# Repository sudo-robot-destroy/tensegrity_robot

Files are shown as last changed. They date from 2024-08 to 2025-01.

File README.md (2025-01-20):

# tensegrity_robot
A repository to track the development of a robot with tensegrity wheels

## Main Design Goals
The main idea is to investigate making a ground vehicle capable of being dropped from a drone without being damaged with the following requirements:
* The vehicle should also be able to drive over rough terrain like high grass, forest floor and climb steps.
* It should also either be able to drive upside down or easily flip itself over.
* The vehicle should be light weight and made using DIY components like off the shelf parts and 3D printing.

## Background
The first design is motivated by [[1]](https://jiefengsun.github.io/pdfs/spiegel2023shape.pdf).
As mentioned in the paper, some shortcomings of their design are sticks get stuck in wheels since they're open, and it tips over easily since there are only two wheels. The first design trial will use similar wheels but will have 4 wheels in a skid steer layout. If stuck sticks are a problem I might look into using closed wheels although I'm not sure if they're work great. 

Construction of tensegrity wheels is detailed in [[2]](http://best.berkeley.edu/wp-content/uploads/2017/09/DETC2017-68264-1.pdf).

## Rough ideas
* The wheels will be TPU and carbon fiber rod.
* The rest of the body will be a combination of carbon fiber rod and 3D printed TPU and PETG parts.  
* The first design will use simple electronics:  
  * an RF receiver
  * 4-in-1 ESC
  * Two brushless motors for drive
  * A single servo for collapsing the wheels?
  * A lipo battery (3s?)

## First design attributes
For the first design, I'll just copy the wheels from [1] as much as possible, here is what they used:  
### Wheels: 
* Carbon rod diameter: 2 mm  
* Carbon rod length (l<sub>r</sub>): 130 mm, 6 rods/wheel so 24 are needed.  
* Rod caps: abrasion-resistant TPU - Cheetah 95 A  
* Rod cap length: 12 mm
* Cable material: TPU - Ninja-flex 85 A  
* Wheel hub material: Nylon-X (carbon fiber-enhanced filament)  
* Cable cross thickness: 1.5 mm  
* Cable width: 1 mm 
* Cable length (printed, 0.9(0.6l<sub>r</sub>)): 70.2 mm  

### Collapsing mechanism:  
* Motor:[Pololu: 1595](https://www.pololu.com/product/1595) (stall torque - 12 kgcm) 
* Cable: Nylon

### Drive train:
* Drive motors: [Pololu: 4794](https://www.pololu.com/product/4794) with 3:1 extra  
* Stall torque: 5.5 kgcm x 3 = 16.5 kgcm
* Drive bearings: [Uxcell: 626-2RS](https://www.amazon.com/uxcell-626-2RS-Bearing-6x19x6mm-Bearings/dp/B07TLKGDJ6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) 
* Battery: 2S Lipo
* Motor driver: [Pololu: 2135](https://www.pololu.com/product/2135) (also used for collapsing) 

## Shopping list
* Carbon fiber rods: [400 mm x 10 from Fielect for $12.99](https://www.amazon.com/Fielect-Diameter-Carbon-Straight-Airplane/dp/B083LC917H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)  
* TPU, 85A: [Siraya Tech Flex TPU for $31.99](https://www.amazon.com/Siraya-Tech-Flex-Filament-Moisture-Resistant/dp/B0CP213ZMG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) 

## Print details
* Rod end-caps
  * 12 per wheel so 48 total...maybe, unless there are special ones that connect to hubs. 
  * No supports
  * Standard .2 profile
  * Profile for tight rod fit starts with a 2mm hole, then a 1 degree draft. The crushed ribs go .25 mm into the 2mm rods. It might be a little too tight, I have to hammer them in.  
  * Currently printed with PLA 
* Cable section
  * TPU 85A
  * Used 3 walls but mainly just to do a solid infill that way. 
  * 8 per wheel? 

## Test prints
Here was the first tensegrity ball I made - I was able to throw it on concrete as hard as I can without any damage:

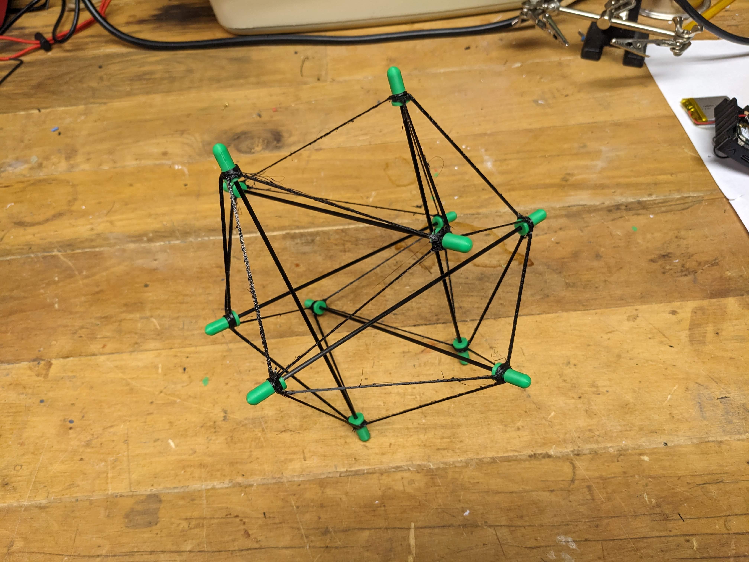
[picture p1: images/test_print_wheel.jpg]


## TO-DOs:
* Buy GT2 belt components
  * wheel span is 200 mm so belts need to be around 100mm each. 
  * 6mm wide
  * 2mm pitch.  
  * It looks like the list them by the outer perimeter. I estimate 243.33 for a 20T pulley so call it 250mm
  * That'd be a 250-2GT-6 belt. Ordered 12Jan2025
  * 20 tooth is the popular small pulley size. 
* Make the wheel hub part
  
## References:
[1] "A Shape-Changing Wheeling and Jumping Robot Using Tensegrity Wheels and Bistable Mechanism" https://jiefengsun.github.io/pdfs/spiegel2023shape.pdf

[2] "Modular Elastic Lattic Platform for Rapid Prototyping of Tensegrity Robots" http://best.berkeley.edu/wp-content/uploads/2017/09/DETC2017-68264-1.pdf

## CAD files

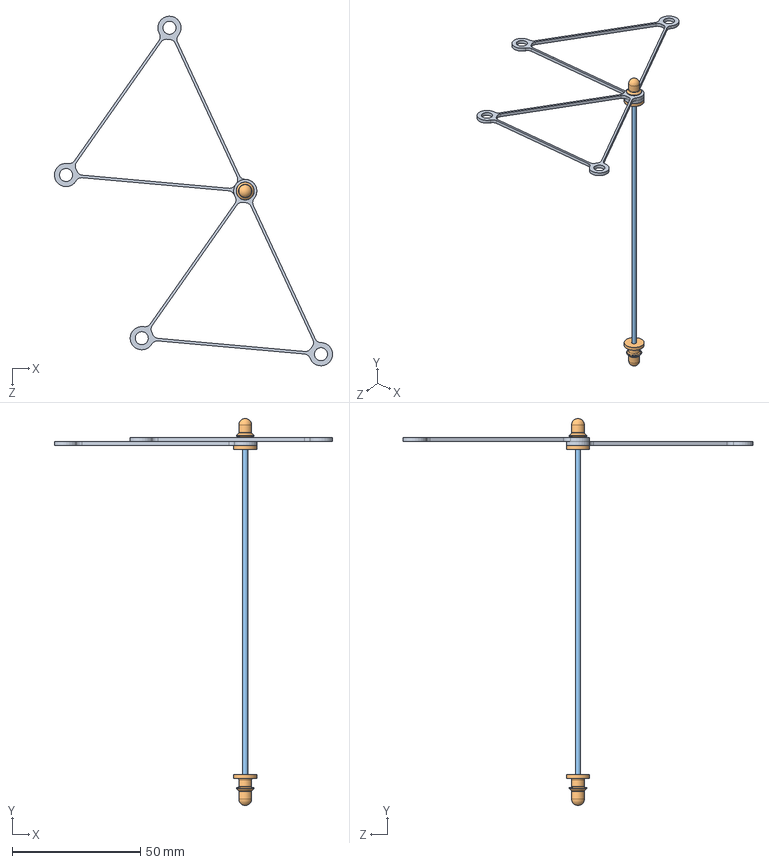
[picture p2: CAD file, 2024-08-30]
developmental_assemblies/rod_end_assembly.SLDASM
108.6 x 151.0 x 136.4 mm
tensegrity_rods_2mm_130mm
rod_end_cap x 2
tensegrity_cable_section x 2

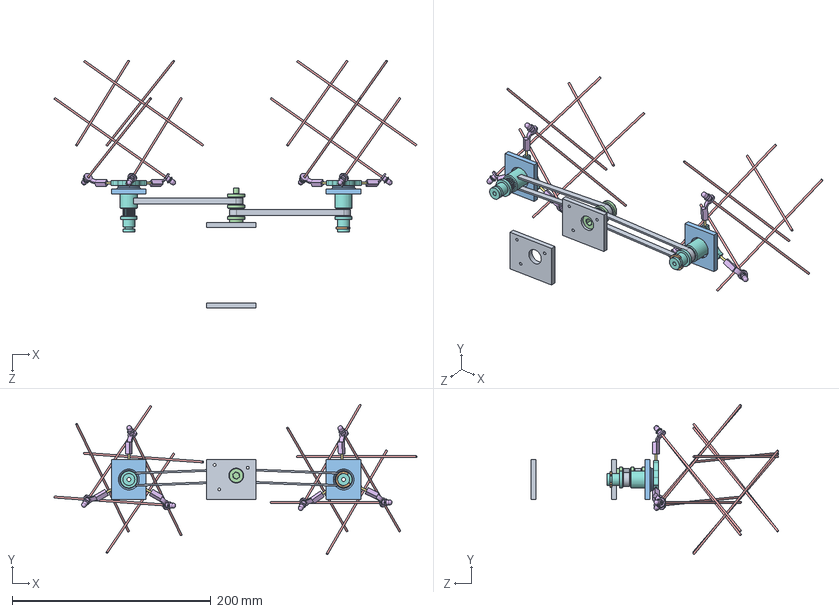
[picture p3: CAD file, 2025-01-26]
main_assembly.SLDASM
365.4 x 151.3 x 249.1 mm
motor_mount_L x 2
wheel_hub x 2
hub_rods_2mm_dia x 6
rod_end_cap_hub x 6
tensegrity_rods_2mm_130mm x 12
gt2_pulley_20T_double
wheel_axle_bearing x 2
custom-98543A116_Side-Mount External Retaining Rings x 2
250-GT2-belt-20Tpulleys x 2

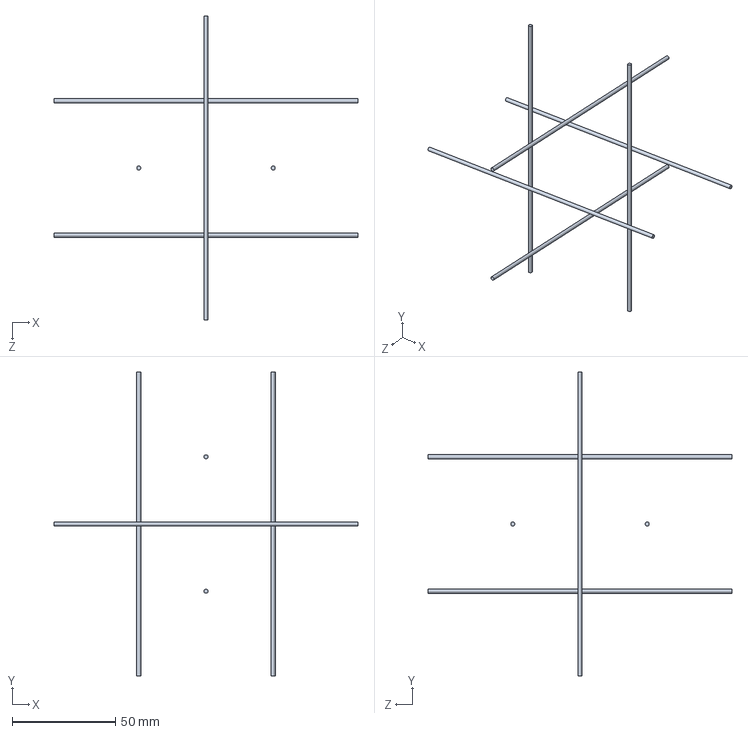
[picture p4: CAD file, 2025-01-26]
wheel_assembly/simple_icosahedron_wheel.SLDASM
147.0 x 147.0 x 147.0 mm
tensegrity_rods_2mm_130mm x 6

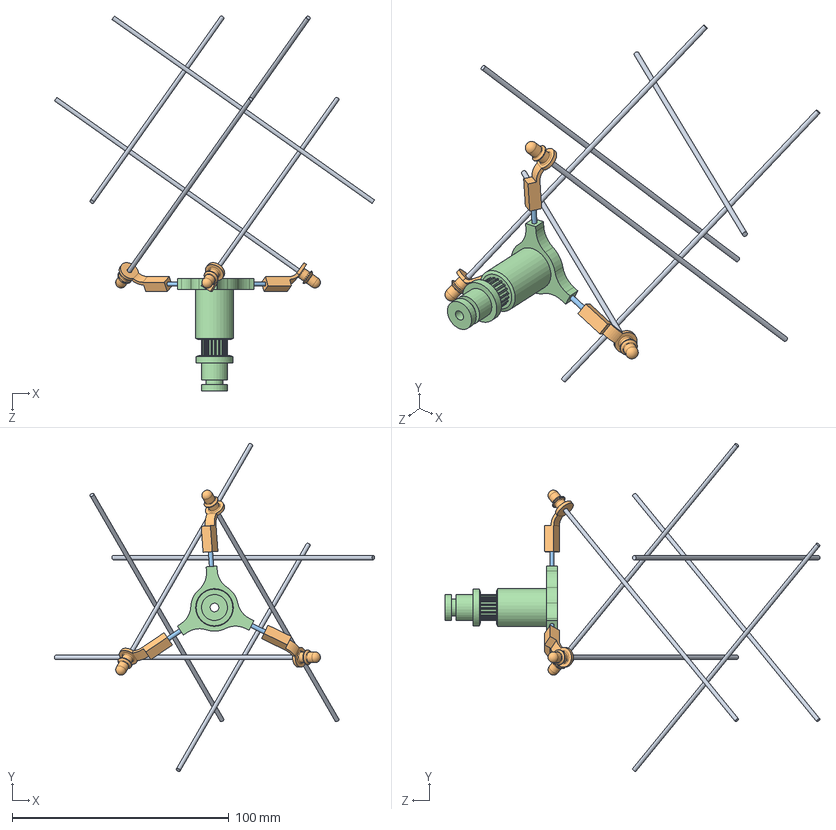
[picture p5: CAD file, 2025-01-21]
wheel_assembly/wheel_assembly.SLDASM
147.7 x 151.3 x 173.0 mm
wheel_hub
hub_rods_2mm_dia x 3
rod_end_cap_hub x 3
tensegrity_rods_2mm_130mm x 6

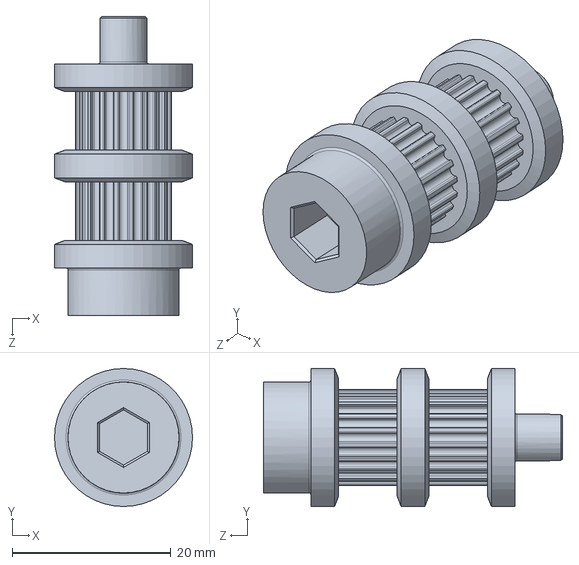
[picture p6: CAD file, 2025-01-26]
custom_parts/gt2_pulley_20T_double.SLDPRT
17.4 x 17.4 x 37.8 mm

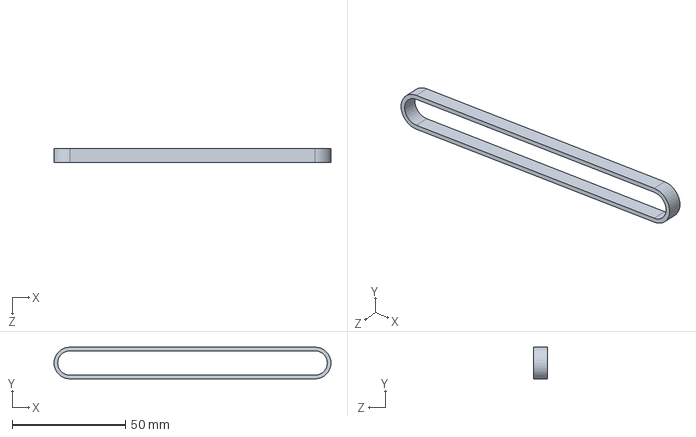
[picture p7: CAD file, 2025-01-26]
drive_train/250-GT2-belt-20Tpulleys.SLDPRT
122.2 x 14.0 x 6.00 mm

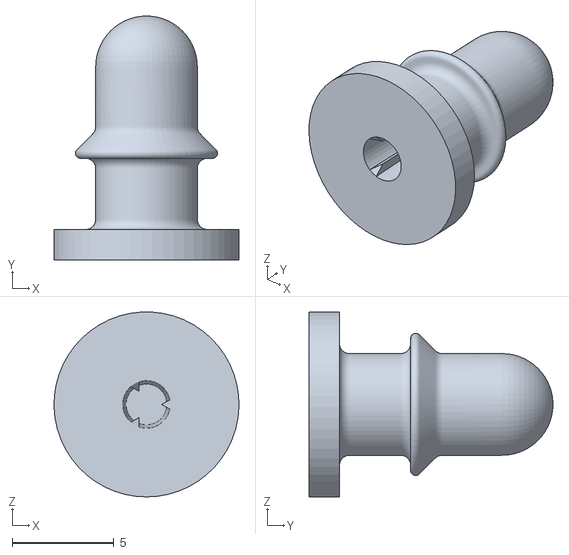
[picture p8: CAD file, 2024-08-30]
print_files/rod_end_cap_one_peice.STL
9.10 x 12.0 x 9.09

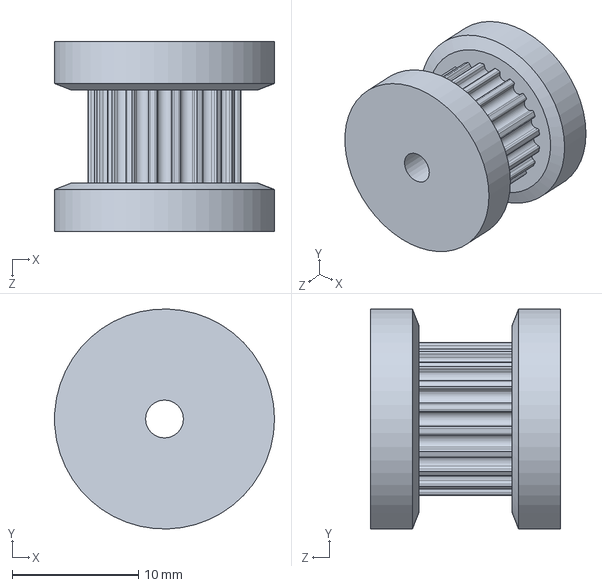
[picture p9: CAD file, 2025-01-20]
custom_parts/gt2_pulley_20T.SLDPRT
17.4 x 17.4 x 15.0 mm

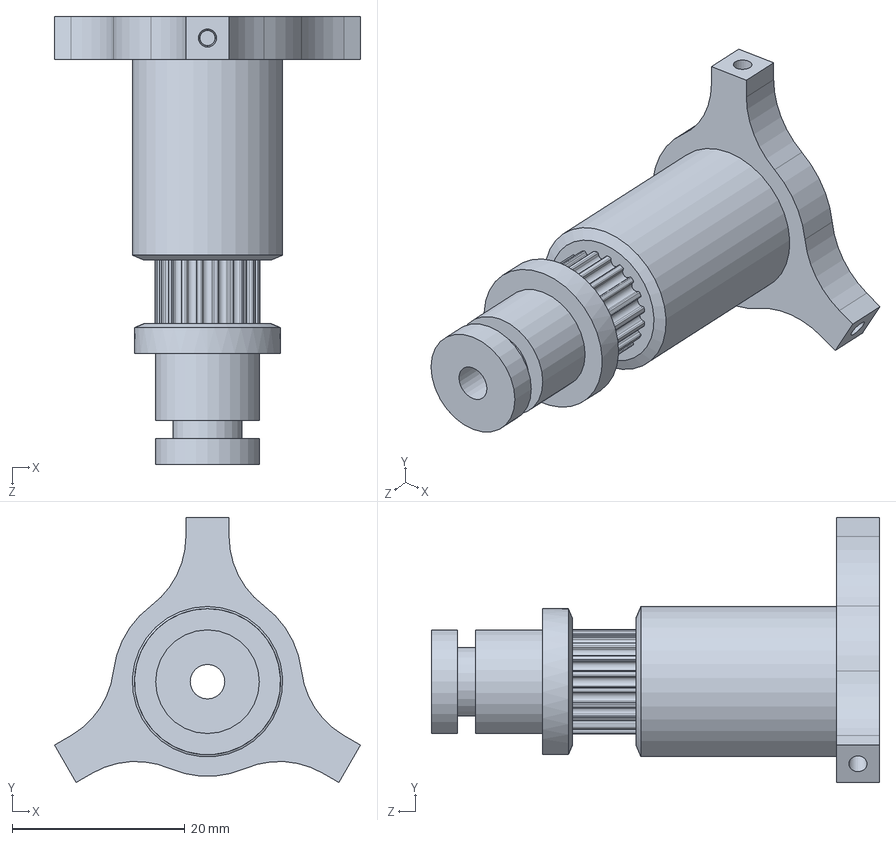
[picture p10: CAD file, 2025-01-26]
drive_train/wheel_hub.SLDPRT
35.4 x 30.7 x 51.9 mm

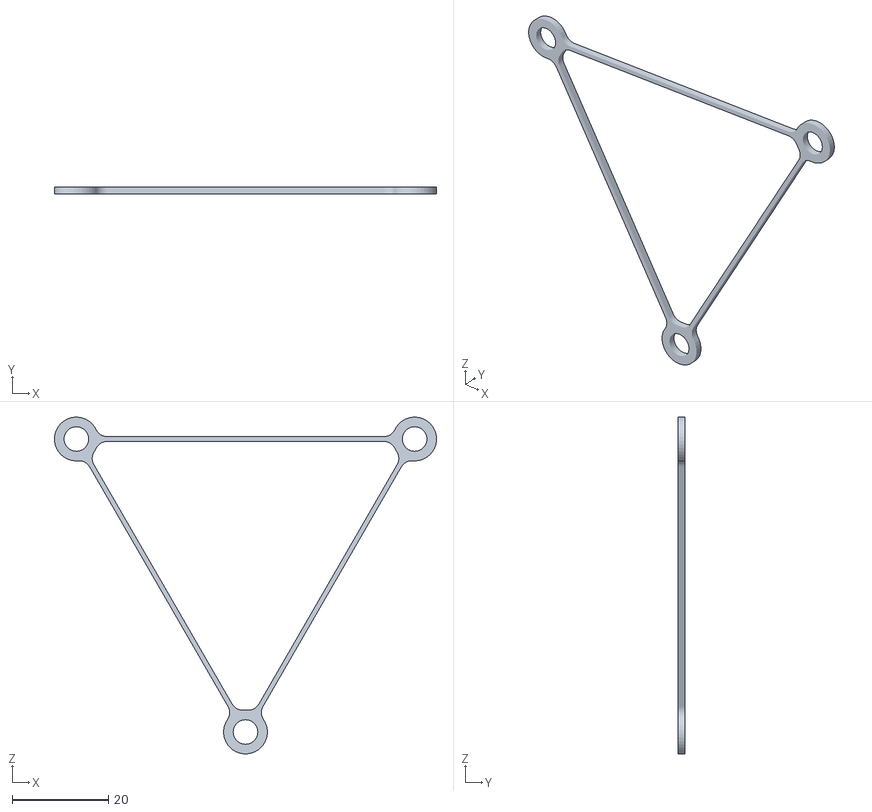
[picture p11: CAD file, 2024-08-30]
print_files/tensegrity_cable_section.STL
79.3 x 1.50 x 69.9

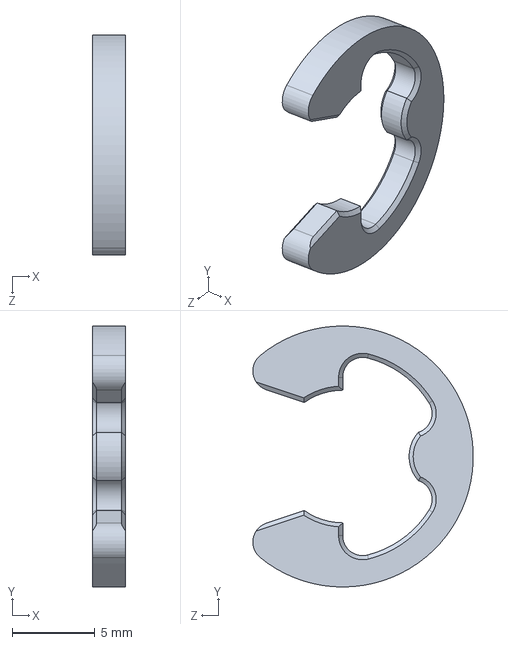
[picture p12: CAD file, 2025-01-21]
drive_train/custom-98543A116_Side-Mount External Retaining Rings.SLDPRT
2.00 x 15.7 x 13.3 mm

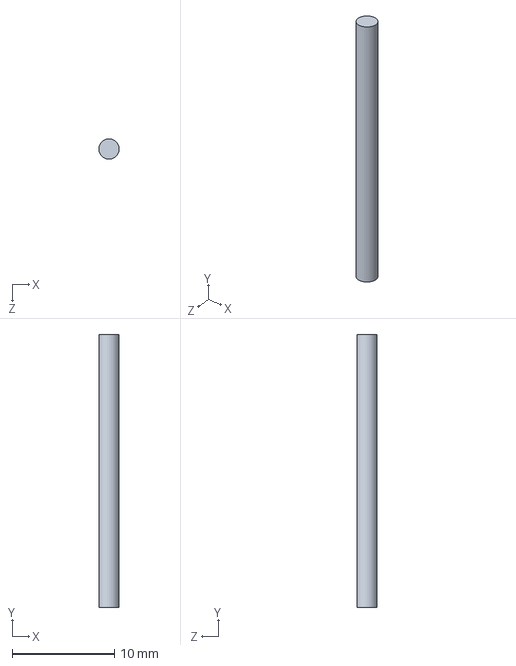
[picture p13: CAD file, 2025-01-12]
wheel_assembly/hub_rods_2mm_dia.SLDPRT
2.00 x 26.8 x 2.00 mm

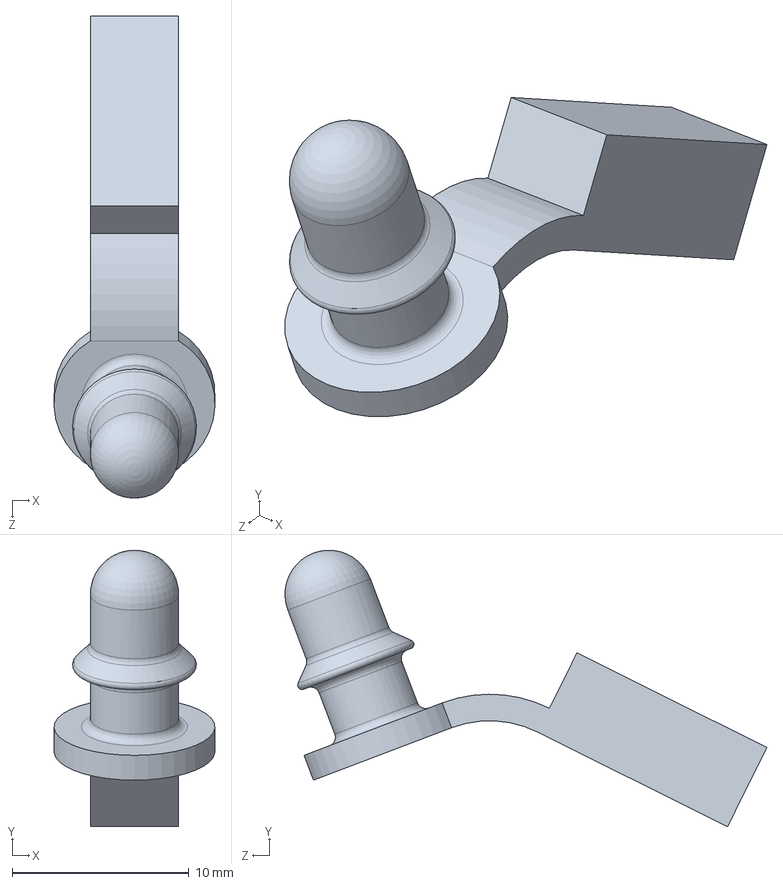
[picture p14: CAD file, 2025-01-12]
wheel_assembly/rod_end_cap_hub.SLDPRT
9.09 x 15.6 x 27.2 mm

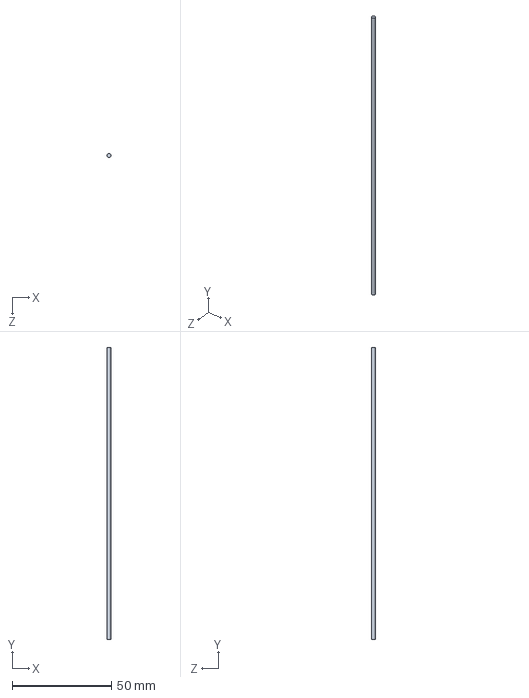
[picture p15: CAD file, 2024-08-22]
custom_parts/tensegrity_rods_2mm_130mm.SLDPRT
2.00 x 147.0 x 2.00 mm

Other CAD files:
custom_parts/rod_end_cap.SLDPRT
custom_parts/tensegrity_cable_section.SLDPRT
drive_train/wheel_axle_bearing.SLDPRT
drive_train/motor_mount_L.SLDPRT
drive_train/drive_pulley_bearing.SLDPRT
drive_train/vac_bot_brush_motor_L.SLDPRT
drive_train/vac_bot_brush_motor_R.SLDPRT
drive_train/wheel_axle_bearing_inner.SLDPRT
drive_train/wheel_clip_washer.SLDPRT
references/3764N107_High-Strength Gt Timing Belt Pulley.SLDPRT

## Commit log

2024-08-19 Add 1st draft cable model
    [tensegrity_cable_section.SLDPRT, tensegrity_cable_section.STL]
2024-08-20 added simple icosahedron model
    [simple_icosahedron_wheel.SLDASM, tensegrity_rods_2mm_130mm.SLDPRT]
2024-08-22 add rod ends
    [rod_end_assembly.SLDASM, rod_end_cap.SLDPRT, simple_icosahedron_wheel.SLDASM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]
2024-08-22 adjust rod cap for printing
    [rod_end_assembly.SLDASM, rod_end_cap.SLDPRT, rod_end_cap.STL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]
2024-08-24 ugh, I dimensioned the cables wrong, its fixed now
    [rod_end_cap.SLDPRT, rod_end_cap.STL, tensegrity_cable_section.SLDPRT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]
2024-08-29 try end cap as one peice
    [rod_end_assembly.SLDASM, rod_end_cap.SLDPRT, rod_end_cap.STL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]
2024-08-29 tiny tweak to one peice end cap
    [rod_end_cap.SLDPRT, rod_end_cap_one_peice.STL]
2024-08-30 beef up rod end cap
    [rod_end_assembly.SLDASM, rod_end_cap.SLDPRT, rod_end_cap_one_peice.STL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]
2024-09-01 add motor calculations in design sheet
2024-09-02 finished motor calculations
2024-10-08 Added motors from vaccume brushes
    [simple_icosahedron_wheel.SLDASM, vac_bot_brush_motor_L.SLDPRT, vac_bot_brush_motor_R.SLDPRT]
2024-10-08 no real change, just fixing 3D mouse
    [vac_bot_brush_motor_L.SLDPRT, vac_bot_brush_motor_R.SLDPRT]
2024-11-27 Added rough motor mount and start assembly file
    [main_assembly.SLDASM, motor_mount_L.SLDPRT, simple_icosahedron_wheel.SLDASM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]
2025-01-12 matured motor mount and mocked up assem.
    [hub_rods_2mm_dia.SLDPRT, main_assembly.SLDASM, rod_end_cap.SLDPRT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]
2025-01-20 Add double drive pulley
    [3764N107_High-Strength Gt Timing Belt Pulley.SLDPRT, drive_pulley_bearing.SLDPRT, gt2_pulley_20T.SLDPRT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]
2025-01-20 worked on wheel axle, not done yet.
    [gt2_pulley_20T_double.SLDPRT, main_assembly.SLDASM, motor_mount_L.SLDPRT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]
2025-01-21 Wheel axel done but need to finish long axel configuration
    [custom-98543A116_Side-Mount External Retaining Rings.SLDPRT, gt2_pulley_20T_double.SLDPRT, main_assembly.SLDASM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]
2025-01-26 Add drive belts
    [250-GT2-belt-20Tpulleys.SLDPRT, gt2_pulley_20T_double.SLDPRT, main_assembly.SLDASM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]
